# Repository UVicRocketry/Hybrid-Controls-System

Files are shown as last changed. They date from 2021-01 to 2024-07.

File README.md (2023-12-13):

# Hybrid-Controls-System (HB - Project Acronym)

## Project Information

UVic Rocketry's hybrid controls system is designed to actuate and monitor the states of stepper motor driven valves located on a high-pressure oxidizer feed system. The controls system includes the following components:
- Mission Control Board (MCB) : A physical panel with toggle switches, momentary buttons, indicator lights, and a buzzer
  - Sends commands to Mission Control Computer based on user input through switches/buttons
- Mission Control Computer (MCC) : The main controller and communication method with the valve cart
  - Manages commands from the MCB and forwards them to the valve cart 
  - Confirms valve status from the valve cart
  - Also able to be used as an override in case the MCB stops working
- Valve Control Cart (VC) : Actuates all valves on the test stand
  - Recieves command from Mission Control Computer
  - Executes valve movements
  - Obtains confirmation or error from limit switches
  - sends confirmed valve states or error back to the Mission Control Computer

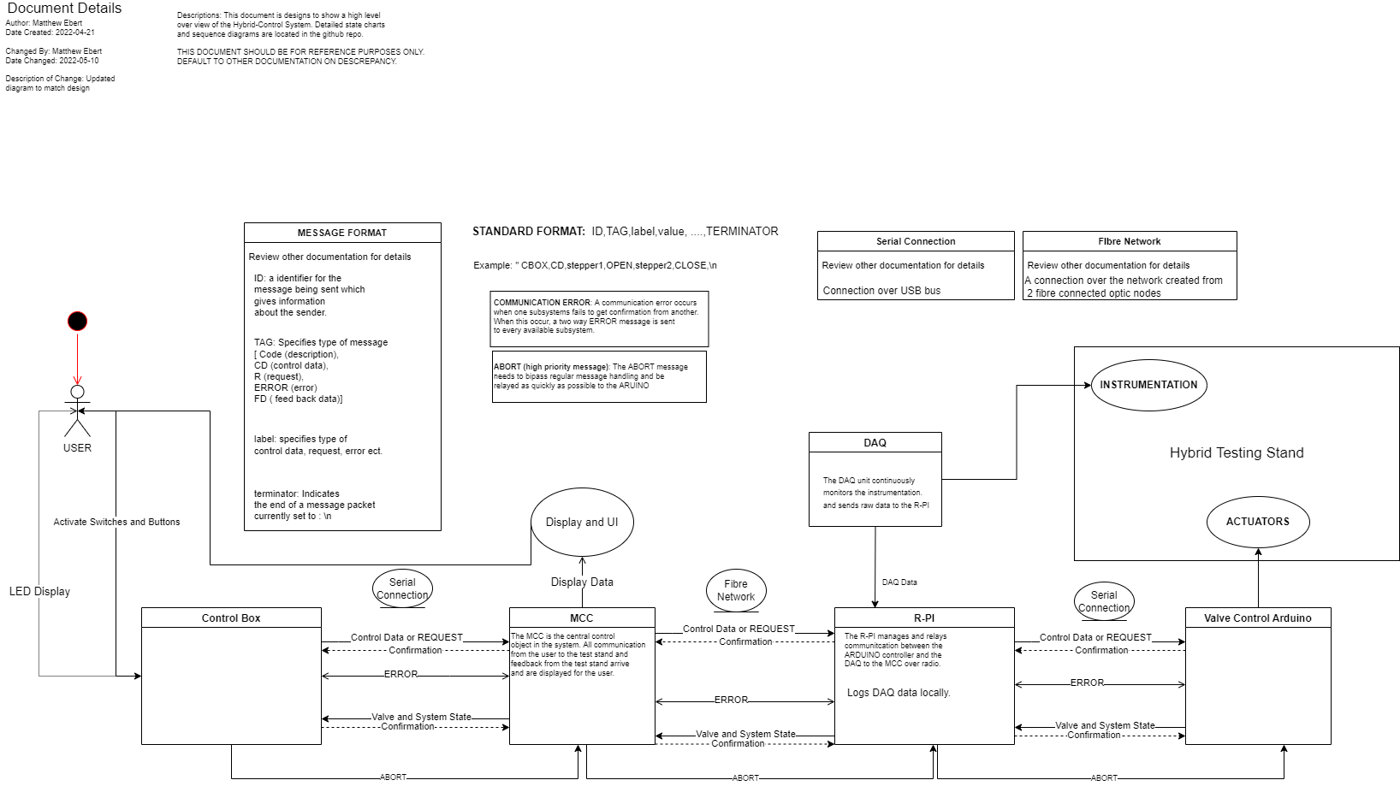
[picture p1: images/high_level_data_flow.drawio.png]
System_Control_Flow_Diagram
  
_Note: If you get the draw.io extension for vs code you can edit this picture directly._
**Possibly out of date and needs review!**

## Installation and Setup of the GUI
The GUI for the Mission Control Computer is the brains of both the Valve Cart and the Mission Control Board, as well as the communication between them. 

There are two options for installing the GUI and communication libraries: downloading a released compiled version, or downloading directly from source and running as a python script.

### Downloading and Running a Release
Releases of the GUI are bundled into a single file using PyInstaller, and built for x86_64 architecture **only**. If you need an x86 version, refer to the compiling from source instructions of this document.

1. To find the latest release, go to <https://github.com/UVicRocketry/Hybrid-Controls-System/releases> and download the executable for your system.

2. Once downloaded, you may need to enable execution of the executable (refer to your system's documentation). On Linux, this is `chmod +x HybridControlsGUI`

3. Finally, just run the GUI by either double-clicking or executing from the terminal.

### Downloading and Running from Source
Running from source is necessary if you want to be bleeding edge, or if there's no release for your system. This method is bit finicky, but if you follow the steps below, you'll be good to go

1. **Make sure you have the right Python version**, you must have Python 3.9 or above for the libraries you need to work.
2. **Install pre-requisites**: Use the following command to install all the pre-requisites you need for the GUI: `pip3 install betterconfigs pyserial PyQt5`
3. **Download from Source**: You can pull the bleeding commit from the git repo using `git pull https://github.com/UVicRocketry/Hybrid-Controls-System.git`
4. **Checkout the right branch**: Make sure you're in the right branch by cd-ing into the git repo you just downloaded and using `git checkout *branchname*` (replace branchname with the right branch name)
5. **Run the GUI**: If you've done everything right, you can run the GUI by cd'ing into `./src/MCC_GUI/` and running `python3 gui_valve.py`. If you get an error, refer to the *Common Errors* section below

## Command Structure Examples
Command structure breakdown:

VC,Command,Modifier,Modifier,etc

EX:

VC,CTRL,MEV,OPEN - opens MEV valve

VC,CTRL,N2OF,CLOSE - closes N2OF valve

VC,STATUS - reports status of all valves

VC,ABORT - initiates abort seequence

## Common Issues & Errors
**If you can open the GUI, and you're having issues with communication, use the debug console to help troubleshoot**
<details><summary>The GUI opened, but I can't see any serial devices to select</summary>
1. Is the device plugged in and receiving power? (It's okay I do it all the time too). Also, try hitting the refresh button.<br>
2. If you're getting power to the device, check the OS's device manager and see if it's showing up. If it is, you might have a permissions error with the applications. Linux especially has this issue (Your user might need to be added to the dialout group).<br>
</details>

<details><summary>I'm not able to run the GUI</summary>
Try running in your terminal and seeing if it gives you any errors. Otherwise, your window manager might not be able to run Qt applications (looking at you GTK+!)
</details>

<details><summary>Pip won't let me install the library betterconfigs</summary>
I've seen this error before, but not really sure why it happens even though the Python version is correct. You can go to PyPi and install manually if it's giving you trouble.
</details>

<details><summary>I'm not sure which branch to pull from</summary>
Ask the maintainers! If you've got access to the Discord, just message @Propulsion and someone should be able to help you out. If nobody knows, probably the latest push is the best.
</details>

<details><summary>It's still broken</summary>
If nobody in propulsion can help, contact <a href="mailto:iainrosen@uvic.ca">iainrosen@uvic.ca</a> and he should be able to help you out!
</details>

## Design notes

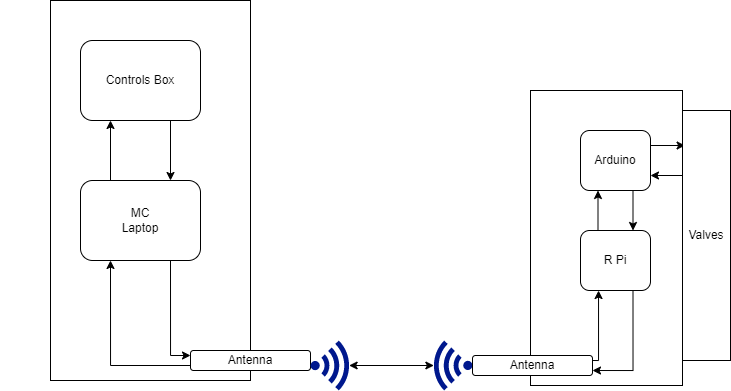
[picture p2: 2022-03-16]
images/system_diagram.png

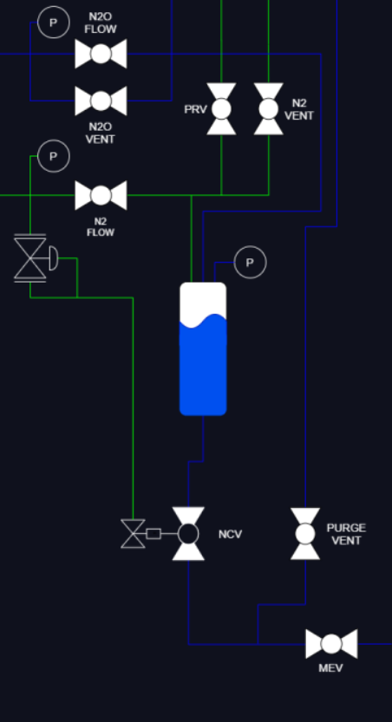
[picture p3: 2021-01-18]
images/MULE-1_PID_for_GUI.png

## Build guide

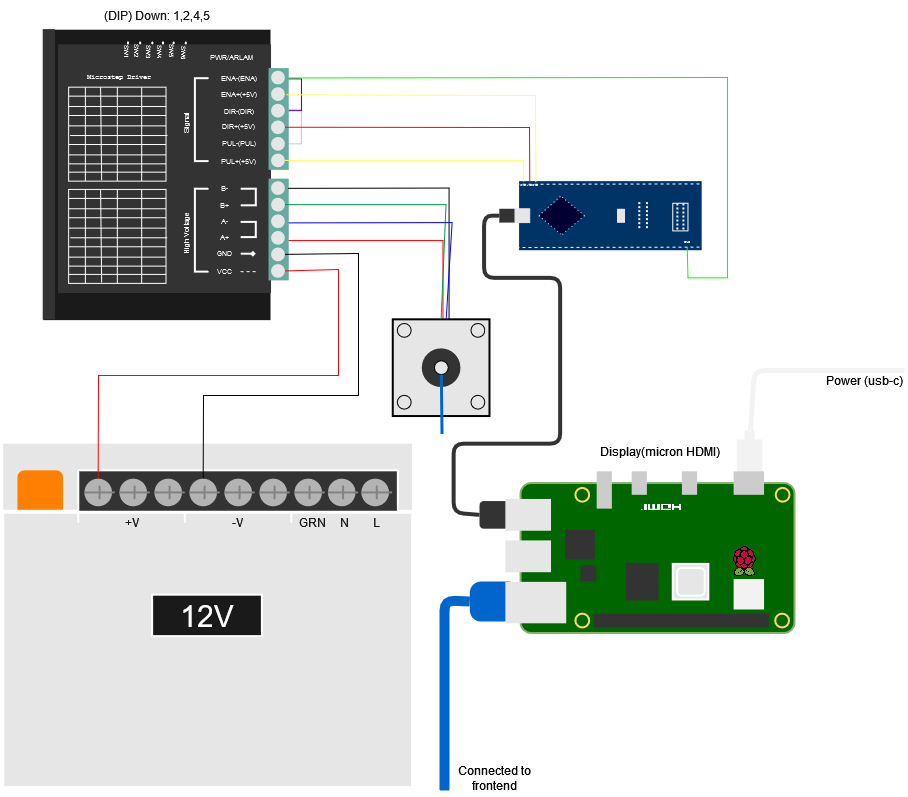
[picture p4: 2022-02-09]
images/ControlsWiringDiagram.drawio.png

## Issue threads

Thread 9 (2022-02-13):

HBPR-4 GUI Updates

Devon-H, 2022-02-13:
The following is a brief list taken from a discussion with Kris and JJ on Feb. 12, 2022.
- fix toggle switches (ask Kris Lemieux)
- Remove feed system schematic
- relocate buttons
- move mission critical buttons (Fire, abort, vent) to physical buttons
- make custom test file type for config

klemie, 2022-02-18:
Might be good to break this up into multiple issues.

Closed 2022-06-22.

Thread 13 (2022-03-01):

HBPR-7 01-03-22 Owen & Devon Meeting

Devon-H, 2022-03-01:
**Description**
Owen and Devon's meeting on March 1st.

To Do:
- organize server and client files into separate folders
- figure out what's happening on arduino side (kris knows)
- figure out what's happening on GUI side (kris knows)
-

**Acceptance Criteria**
 <Write specifically what is need for this issue to be completed>

**Dev Notes**
[for assignee]<write down your thought process when developing this issue>

**Linked issues**
 <If there are any related issues>

<Add to milestone>

Closed 2022-06-22.

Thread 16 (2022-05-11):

HBPR-8 Mission Control Box

ByonicTao, 2022-05-11:
**Description**
 Firmware for arduino with proper input gathering, comm with MCC, and data display. Along with schematic for the circuit.

**Acceptance Criteria**
 Firmware can communicate with computer properly, and display the data. Also includes an accurate schematic of the circuit.

**Dev Notes**
3rd version of LED circuit. Didn't work with back driving the switch inputs, as some LEDs would stay on  constantly and others would not turn on. Then there was discussion of wiring the LEDs up to output pins directly. This was decided against because of need to add additional things to the box, including a buzzer and potentially more signaling devices. Currently the implementation is going to use shift registers to run the LEDs which will leave plenty of room for other things to run off the digital pins and remove the flickering that would result from using an methods that uses persistence of vision.

Closed 2022-06-22.

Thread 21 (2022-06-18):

HBPR-10 On-stand Controls

OwenBC, 2022-06-18:
**Description**
 <Describe what the feature or bug that need to be resolved>
 <Description of the big component that encompasses the issue working on>
 <Depencies, ex. libraries, sensors, hardware, small parts of code youhave to work on>
 <ow to do the things>

**Acceptance Criteria**
 <Write specifically what is need for this issue to be completed>

**Dev Notes**
[for assignee]<write down your thought process when developing this issue>

**Linked issues**
 <If there are any related issues>

<Add to milestone>

Closed 2023-05-13.

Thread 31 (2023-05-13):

VCA Testing

iainrosen, 2023-05-13:
Verify the valves on the VCA are responding and moving correctly

iainrosen, 2023-06-09:
- Stepper for N20V is unresponsive, checked pin out from Arduino and all connected correctly. Limits working.

iainrosen, 2023-06-09:
Tested and working:
- N2F
- N20F
- ERV
- MEV

iainrosen, 2023-06-09:
NCV when trying to use CTRL throws a BADVAL error. Possibly not programmed for actuation?

iainrosen, 2023-06-09:
We have no way of telling where RTV is, need to talk to Devon about this.

Closed 2023-07-20.

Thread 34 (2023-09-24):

Update serial communication to new library

iainrosen, 2023-09-24:
Serial communication needs to be hauled over a bit using a new library with checksumming and implementation of duplicate message elimination

This will improve:
- Serial connections over long ranges with ethernet (which experience some issues in translation)
- Serial connections over radio, which will be used eventually to control the valve cart from afar for hot fire tests

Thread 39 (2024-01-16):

Message Parsing Issues

iainrosen, 2024-01-16:
Messages don't parse correctly, VC is sending separate format from MCC GUI

iainrosen, 2024-02-06:
The method of parsing switch states seems to be correct, going to test with the Valve Cart and see if error is replicated.

See lines 81-87 of commlib.py

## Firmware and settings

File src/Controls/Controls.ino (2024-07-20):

/*  Valve Cart and Feed System: Controls - Valve Controls - Rework V 1.1
   Author(s):
   Matthew Ebert
   Logan Sewell
   JJ
   Joshua Piuti
   Organization: UVic Rocketry
*/
#include "Valve.h"

//*********Limit Pins*********
#define OpenLimitMEV 30
#define CloseLimitMEV 27
#define OpenLimitN2OV 41
#define CloseLimitN2OV 40
#define OpenLimitRTV 39
#define CloseLimitRTV 38
#define OpenLimitN2F 42
#define CloseLimitN2F 43
#define OpenLimitERV 34
#define CloseLimitERV 35
#define OpenLimitN2OF 33
#define CloseLimitN2OF 32
#define OpenLimitNCV 28
#define CloseLimitNCV 29
//****************************

//******Enable Pins **********
#define N2OFEnab 46
#define N2OVEnab 47
#define N2FEnab 49
#define ERVEnab 50
#define MEVEnab 51

//*********Driver Pins********
#define StepMEV 19
#define DirMEV  20
#define StepN2OV 4
#define DirN2OV  3
#define StepN2F 10
#define DirN2F  9
#define StepERV 15
#define DirERV  14
#define StepN2OF 17
#define DirN2OF  16
//****************************

//***Solenoid & Igniter Pins***
#define Igniter 45
#define Solenoid 48
#define RTVEnab 37
//****************************

//*********Safety Pins********
#define KeySwitch 5
#define EStop 6
//****************************


int IgniterState = 0;
int TargetState [9];

void MoveToTarget();
void setTarget (String valveCommands);
String readCSV(String * rxBuf);
void sendState (void);

bool ABORT = false;
//Assining Valves
//Stepper Valves
Valve N2F = Valve(OpenLimitN2F, CloseLimitN2F, StepN2F, DirN2F, 20);
Valve N2OV = Valve(OpenLimitN2OV, CloseLimitN2OV, StepN2OV, DirN2OV, 4);
Valve N2OF  = Valve(OpenLimitN2OF, CloseLimitN2OF, StepN2OF, DirN2OF, 4);
Valve ERV  = Valve(OpenLimitERV, CloseLimitERV, StepERV, DirERV, 2);
Valve MEV  = Valve(OpenLimitMEV, CloseLimitMEV, StepMEV, DirMEV, 4);

//Other Valves
Valve NCV  = Valve(OpenLimitNCV, CloseLimitNCV);
Valve RTV  = Valve(OpenLimitRTV, CloseLimitRTV, RTVEnab);

void setup() {
  // Sets Limit Pins
  //enable set up
  pinMode(N2OFEnab, OUTPUT);
  pinMode(N2OVEnab, OUTPUT);
  pinMode(N2FEnab, OUTPUT);
  pinMode(ERVEnab, OUTPUT);
  pinMode(MEVEnab, OUTPUT);

  //Currently does not effect motors??
  digitalWrite(N2OFEnab, HIGH);
  digitalWrite(N2OVEnab, HIGH);
  digitalWrite(N2FEnab, HIGH);
  digitalWrite(ERVEnab, HIGH);
  digitalWrite(MEVEnab, HIGH);

  //Unsure how these operate
  pinMode(Solenoid, OUTPUT);
  digitalWrite(Solenoid, LOW);
  pinMode(Igniter, OUTPUT);
  digitalWrite(Igniter, LOW);
  //********************

  //Sets up EStop and Keyswitch
  pinMode(EStop, INPUT_PULLUP);
  pinMode(KeySwitch, INPUT_PULLUP);


  //Serial_Startup
  Serial.begin(115200);
  //time in ms the serial blocks waiting for data
  Serial.setTimeout(10);
  //*********************************************

  Serial.println("VC,STATUS,STARTUP,SUCCESS");
  Serial.println("VC,CF,Initalizing_to_safe_state:(ALL Closed)");
  sendState();
  delay(1000);
  //Set all target states to closed
  for(int i = 0; i<9; i++)
  {
    TargetState[i] = 1;
  }
}


void loop() {
  
  if (Serial.available() || digitalRead(EStop) == HIGH)
  {//if a message has been recieved
    //read all serial data
    String rxBuffer = Serial.readString();
    /*Should the buffer be cleared before entire message is sent/recieved
    a fragment will be created and not parsed. An end flag should be checked
    to ensure this case does not occur.*/
    String Command = "";
    String TYPE = "";
    String SOURCE = "";
    //read source of data
    SOURCE = readCSV(&rxBuffer);
    //read type of data
    TYPE = readCSV(&rxBuffer);
    //Send acknolodgement
    //CCSerial.println("VC,ACK,");
    /* Currently there is no error correcting or proper acknoledgement handling
    This ACK is for debugging only. Proper protocols should be developed to ensure
    a message is handled properly*/
    if (TYPE == "UNABORT" && ABORT)
    {
      Serial.println("VC,STATUS,CANCELLED ABORT");
      ABORT = false;
    } else if (TYPE == "ABORT" || ABORT == true || digitalRead(EStop) == HIGH)
    {
      ABORT = true;
      //Serial.println(TYPE);
      Serial.println("VC,STATUS,ABORTED");
      digitalWrite(Igniter, LOW);
      digitalWrite(Solenoid, LOW);

      //implement abort code
      TargetState[0] = 1;  //Close N2OF
      TargetState[1] = -1; //Open N2OV
      TargetState[2] = 1;  //Close N2F
      TargetState[3] = -1; //Open Relief Valve
      TargetState[4] = 1;  //Close MEV
      TargetState[5] = 1;  //Close RTV
      TargetState[6] = 1;  //Close Igniter
      TargetState[7] = 1;  //Close NCV
      
    } else if (TYPE == "CTRL")
    {
      //Serial.println(TYPE);
      setTarget(rxBuffer);
    } else if (TYPE == "CONNECT")
    {
      Serial.println("VC,STATUS,ESTABLISH");
      sendState();
    } else if (TYPE == "SUMMARY")
    { 
      //Serial.println(TYPE);
      sendState();
    } else
    {
      Serial.println("VC,ERROR,UNKNOWNCOMMAND," + SOURCE + "," + TYPE + "," + Command);
    }
  }

  //called every loop to step motors if necessary
  //disabled by keyswitch lockout on VC unless being aborted
  if(digitalRead(KeySwitch) == LOW || ABORT)  {
    MoveToTarget();
  }
}


/***********FUNCTIONS*******************/


void sendState (void)
{
  Serial.print("VC,SUMMARY");
  Serial.print(",N2OF," +  N2OF.strState());
  Serial.print(",N2OV," +  N2OV.strState());
  Serial.print(",N2F," +  N2F.strState());
  Serial.print(",RTV," +  RTV.solStrState());
  Serial.print(",ERV," +  ERV.strState());
  Serial.print(",MEV," +  MEV.strState());
  Serial.print(",NCV," +  NCV.strState());
  Serial.println("");
}


String readCSV (String * rxBuf)
{
  String Command = "";
  char c;
  c = (*rxBuf)[0];
  while (c != '\n' && c !=  ',' && (*rxBuf).length() > 1) {
    Command += c;
    (*rxBuf).remove(0, 1);
    c = (*rxBuf)[0];
  }
  (*rxBuf).remove(0, 1);
  return Command;
}


void setTarget (String valveCommands)
{
  String Label = "";
  String Value = "";
  int index = 0;
  while (valveCommands.length() > 1)
  {
    Label = readCSV(&valveCommands);
    Value = readCSV(&valveCommands);


    if (Label == "N2OF")
    {
    } else   if (Label ==  "N2OV")
    {
      index = 1;
    } else if (Label ==  "N2F")
    {
      index = 2;
    } else if (Label ==  "ERV")
    {
      index = 3;
    } else if (Label ==  "MEV")
    {
      index = 4;
    } else if (Label ==  "RTV")
    {
      index = 5;
    } else if (Label ==  "IGPRIME")
    {
      index = 6;
    } else if (Label == "NCV")
    {
      index = 7;
    } else
    {
      index = 8;
      Serial.println("VC,ERROR,UNKOWNVALVE");
    }

    if (Value == "OPEN")
    {
      TargetState[index] = -1;
    }
    else if (Value == "CLOSE")
    {
      TargetState[index] = 1;
    } else
    {
      TargetState[index] = 0;
    }

  }
}





void MoveToTarget()
{

  if ( N2OF.state() != TargetState[0] && TargetState[0]!=0)
  {    
    N2OF.moveStep(TargetState[0]);
  }
  if ( N2OF.getChange())
  {
    sendState();
  }

  if ( N2OV.state() != TargetState[1] && TargetState[1]!=0)
  {
   N2OV.moveStep(-TargetState[1]);
  }
  if ( N2OV.getChange())
  {
    sendState();
  }

  if ( N2F.state() != TargetState[2] && TargetState[2]!=0)
  {
    N2F.moveStep(TargetState[2]);
  }
  if ( N2F.getChange())
  {
    sendState();
  }

  if ( ERV.state() != TargetState[3] && TargetState[3]!=0)
  {
    ERV.moveStep(-TargetState[3]);
  }
  if ( ERV.getChange())
  {
    sendState();
  }

  if ( MEV.state() != TargetState[4] && TargetState[4]!=0)
  {
    MEV.moveStep(-TargetState[4]);
  }
  if ( MEV.getChange())
  {
    sendState();
  }


  if (RTV.solState() != TargetState[5] && TargetState[5]!=0)
  {
    RTV.moveSol(TargetState[5]);   
    sendState();     
  }
  
  if (IgniterState != TargetState[6] && TargetState[6]!=0)
  {
    if (TargetState[6] == 1)
    {
      digitalWrite(Igniter, LOW);
      IgniterState = 1;
    } else if (TargetState[6] == -1) {
      digitalWrite(Igniter, HIGH);
      IgniterState = -1;
    }
  }

  if (NCV.state() != TargetState[7] && TargetState[7]!=0)
  {
    if (TargetState[7] == 1)
    {
      digitalWrite(Solenoid, LOW);
    } else if (TargetState[7] == -1)
    {
      digitalWrite(Solenoid, HIGH);
    }
  }
  if (NCV.getChange())
  {
    sendState();
  }
}

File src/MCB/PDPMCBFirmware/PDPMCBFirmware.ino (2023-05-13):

/* UVR Propulsion Development Platform Mission Control Box Firmware
  Matthew Ebert
  2023-FEB-01

  This firmware controls the mission control box, gathering input from the switches and buttons, sending them to the controls computer

  This program only sends data on a STATE CHANGE.

  Limited logic should be implemented here.
  The idea is to create a simple controller for the attached computer (MCC)
*/


/***************DEFINITIONS ******************/


/*************PINS and MASKS**************/
#define pinBUZ 11
#define pinABORT 2
#define maskABORT (1<<pinABORT)
#define pinARMKEY 3
#define maskARMKEY 1<<pinARMKEY
#define pinIGFIRE 4
#define maskIGFIRE (1<<pinIGFIRE)
#define pinIGPRIME 5
#define maskIGPRIME (1<<pinIGPRIME)
#define maskPC 0x3F
#define maskPD 0xF0



/**************STRING OUTPUT FORMAT*******************/
#define numValves 9
String listValves[numValves] = {"MEV", "IGPRIME", "IGFIRE", "EVV", "NCV", "RTV", "N2F", "N2OV", "N2OF"};
//String listValves[numValves] = ("N2OF", "N2OV", "N2F", "RTV", "NCV", "EVV", "IGPRIME", "IGFIRE", "MEV");

/****************TYPES******************/
enum status_t {
  DISARMED,//0
  ARMED,//1
};


/**************GLOBALS****************/

volatile bool ABORT = false;
volatile status_t CurSTATUS = NULL;
volatile uint16_t CurState = NULL;




void setup() {
  Serial.begin(115200);
  
  while (!Serial) {};

  Serial.setTimeout(100);
  Serial.flush();
  Serial.print("MCB,STATUS,STARTUP\n");
  cli();
  //sets pinmodes
  DDRD = 0x00;
  DDRC = 0x00;
  DDRB |= 0x04;
  digitalWrite(11, 0);
  abortSetup();
  buzzerSetup();

  PCICR |= B00000100; // Enable interrupts on PD port
  PCMSK2 |= B00101000;
  sei();
  delay(100);
}//setup




void loop()
{

  CurState = getState();
  uint16_t NewState = CurState;
  CurSTATUS = getSTATUS();
  if (CurSTATUS == DISARMED) Serial.print("MCB,STATUS,DISARMED\n");
  if (CurSTATUS == ARMED)
  {
    Serial.print("MCB,STATUS,ARMED\n");
    sendStates(NewState);
  }
  status_t NewSTATUS = CurSTATUS;



  while (!ABORT)
  {


    if (Serial.read() > 0)
    {
      if (CurSTATUS == DISARMED)
      {
        if (CurSTATUS == DISARMED) Serial.print("MCB,STATUS,DISARMED\n");
        return;
      } else
      {
        if (CurSTATUS == ARMED) Serial.print("MCB,STATUS,ARMED\n");
        sendStates(CurState);
      }
   
    }

    NewSTATUS = getSTATUS();
    delay(50);//debounce
    if (NewSTATUS == getSTATUS())
    {
      if (NewSTATUS != CurSTATUS)
      {
        CurSTATUS = NewSTATUS;
        if (CurSTATUS == DISARMED) Serial.print("MCB,STATUS,DISARMED\n");
        if (CurSTATUS == ARMED) Serial.print("MCB,STATUS,ARMED\n");
      }//IF CHANGE STATUS
    }//IF DEBOUNCE



    if (CurSTATUS)
    {
      NewState = getState();
      delay(50);//debounce
      if (NewState == getState())
      {
        if ((NewState != CurState))
        {
          if (getSTATUS())
          {
            sendStates(NewState);
            CurState = NewState;
          }
        }//IF CHANGE STATE
      }//IF DEBOUNCE
    }//IF STATUS

    
  }//WHILE !ABORT




//When ABORT PRESSED
  while (1)
  {
    Serial.print("MCB,ABORTED\n");
    delay(100);
  }

}//loop


//Functions
//-----------------------------------------------------------------------------------------------


uint16_t getState(void)
{
  uint16_t state = ((PIND & maskPD) >> 4) + ((PINC & maskPC) << 4);
  //Serial.print("Registers: ");
  //Serial.println(state);
  return state;
}


status_t getSTATUS(void)
{
  if ((PIND & maskARMKEY) == 0)
  {
    return ARMED;
  } else
  {
    return DISARMED;
  }
}



void sendStates(uint16_t tempState)
{
  Serial.print("MCB,SUMMARY,");

  for (int i = 0; i < numValves; i++)
  {
    Serial.print(listValves[i]);
    Serial.print(",");
    if (tempState & 0x01)
    {
      Serial.print("CLOSE");
    } else
    {
      Serial.print("OPEN");
    }
    tempState = tempState >> 1;
    if(!(i==numValves-1)){
      Serial.print(",");
    }
    
  }
  Serial.print("\n");
}



void abortSetup(void)
{

  EIMSK |= 0x01;//Enable INT0 on D2
  EICRA |= _BV(ISC00) | _BV(ISC00);

}

void buzzerSetup(void)
{
 
  TCCR1A = 0;// set entire TCCR1A register to 0
  TCCR1B = 0;// same for TCCR1B
  TCNT1  = 0;//initialize counter value to 0
  // set compare match register for 1hz increments
  OCR1A = 10000;
  // turn on CTC mode
  TCCR1B |= _BV(WGM12);
  // Set CS10 and CS12 bits for 1024 prescaler
  // TCCR1B |= (1 << CS12) | (1 << CS10);
  // enable timer compare interrupt
  TIMSK1 |= _BV(OCIE1A);
}


ISR(TIMER1_COMPA_vect)
{
  analogWrite(11, 0);
  TCCR1B &= !_BV(CS12) & !_BV(CS10);
}


ISR (PCINT2_vect) {
  delay(50);
  if ((PIND & maskIGPRIME) == 0)
  {
    digitalWrite(pinBUZ, 1);
    TCNT1 = 0;
    TCCR1B |= _BV(CS12) | _BV(CS10);
  }

  
  if (((PIND & maskARMKEY) == 0) && (CurSTATUS == DISARMED))
  {
    digitalWrite(pinBUZ, 1);
    TCNT1 = 0;
    TCCR1B |= _BV(CS12) | _BV(CS10);
  }
}


ISR(INT0_vect)
{

  for (int i = 0; i < 1000; i++)
  {
    if ((PIND & maskABORT) == 0)
    {
      return;
    }
  }
  if ((PIND & maskABORT) > 0)
  {
    ABORT = true;
    Serial.print("MCB,ABORT,\n");
    digitalWrite(pinBUZ, 1);
    TCNT1 = 0;
    TCCR1B |= _BV(CS12) | _BV(CS10);
  }
}

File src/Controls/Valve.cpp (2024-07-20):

#include "Arduino.h"
#include "Valve.h"

// Constructor
Valve::Valve(int OpenLimit, int CloseLimit) {
  this->OpenLimit = OpenLimit;
  this->CloseLimit = CloseLimit;
  this->change = 0;
  this->prevState = 0;//!digitalRead(OpenLimit) | !digitalRead(CloseLimit);
  pinMode(OpenLimit, INPUT_PULLUP);
  pinMode(CloseLimit, INPUT_PULLUP);
}

Valve::Valve(int OpenLimit, int CloseLimit, int StepPin, int DirPin, int StepSpeed) {
  this->OpenLimit = OpenLimit;
  this->CloseLimit = CloseLimit;
  this->StepPin = StepPin;
  this->DirPin = DirPin;
  this->StepSpeed = StepSpeed;
  this->change = 0;
  this->prevState = 0;//!digitalRead(OpenLimit) | !digitalRead(CloseLimit);
  pinMode(OpenLimit, INPUT_PULLUP);
  pinMode(CloseLimit, INPUT_PULLUP);
  pinMode(DirPin, OUTPUT);
  pinMode(StepPin, OUTPUT);
  StepTime = millis();
}

Valve::Valve(int OpenLimit, int CloseLimit, int SolEnab) {
  this->OpenLimit = OpenLimit;
  this->CloseLimit = CloseLimit;
  this->SolEnab = SolEnab;
  this->change = 0;
  this->activated = 1;
  this->prevState = 0;//!digitalRead(OpenLimit) | !digitalRead(CloseLimit);
  pinMode(OpenLimit, INPUT_PULLUP);
  pinMode(CloseLimit, INPUT_PULLUP);
  pinMode(SolEnab, OUTPUT);
  digitalWrite(SolEnab, LOW);  
}

//*********State functions*********
int Valve::state() {
  if (digitalRead(OpenLimit) == LOW) {
    change = (prevState != -1);
    prevState = -1;
    return -1;
  } else if (digitalRead(CloseLimit) == LOW) {
    change = (prevState != 1);
    prevState = 1;
    return 1;
  } else {
    change = (prevState != 0);
    prevState = 0;
    return 0;
  }
}

int Valve::solState() {
  if(activated == 1) {
    change = (prevState != 1);
    prevState = 1;
    return 1;
  } else if (activated == -1) {
    change = (prevState != -1);
    prevState = -1;
    return -1;
  } else {
    change = (prevState != 0);
    prevState = 0;
    return 0;
  }
}

String Valve::strState() {
  if (digitalRead(OpenLimit) == LOW) {
    change = (prevState != -1);
    prevState = -1;
    return "OPEN";
  } else if (digitalRead(CloseLimit) == LOW) {
    change = (prevState != 1);
    prevState = 1;
    return "CLOSE";
  } else {
    change = (prevState != 0);
    prevState = 0;
    return "TRANSIT";
  }
}

String Valve::solStrState() {
  if(activated == 1) {
    change = (prevState != 1);
    prevState = 1;
    return "CLOSE";
  } else if (activated == -1) {
    change = (prevState != -1);
    prevState = -1;
    return "OPEN";
  } else {
    change = (prevState != 0);
    prevState = 0;
    return "TRANSIT";    
  }
}

bool Valve::moveStep(int Dir)
{ 
  //Serial.print("Stepping Pin:");
  //Serial.println(StepPin);
  if ((millis() - StepTime) > StepSpeed)
  {
    //Serial.println(millis());
    //Serial.println(StepTime);
    //Serial.println(millis()-StepTime);
     if(Dir==1)
    {
       digitalWrite(DirPin, 1);
    }else
    {
      digitalWrite(DirPin, 0);
    }
    delayMicroseconds(50);
    digitalWrite(StepPin, 1);
    delayMicroseconds(50);
    digitalWrite(StepPin, 0);
    StepTime=millis();
    return true;
    
  }else if(StepTime>millis())
  {
    //overflow of 32bit millis number
    StepTime=millis();
  }
  return false;
}

bool Valve::moveSol(int State)
{
  if (State == 1)
  {
    digitalWrite(SolEnab, 0);
    activated = 1;
  } else
  {
    digitalWrite(SolEnab, 1);
    activated = -1;
  }
  return true;
}

//*********Getters*********
int Valve::getOpenLimit() {
  return this->OpenLimit;
}

int Valve::getCloseLimit() {
  return this->CloseLimit;
}


int Valve::getChange() {
  return change;
}

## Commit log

2020-10-17 created the framework of the controller file
2020-10-22 Buttons update system states. GUI Fixes
2020-12-18 Controller receiver class implementation
    Created the receiver class in controller.py, this will be in charge of connecting to, and sending and receiving data form the server
2020-12-31 Added manual checkboxs backend and schematic files
2021-01-11 Added AUTO control buttons and bugfixes
2021-01-15 Changed check boxes to toggle switches
2021-01-29 Added the state update method and thread.
2021-02-04 Changed VV to N2 flow
2021-02-23 Fixes schematic png
2021-02-27 Quick exception catch
    Fixed an error in server.py that caused the thing to crash when you hit the disconnect button
2021-03-04 setup for arduino file
2021-03-04 flash LED
2022-02-09 Arduino changes
2022-02-18 arduinoController structure see PR comment
2022-03-16 Revised control logic overview
    Now encompasses the whole system. Still needs a lot of work to properly document what's happening at every stage in the system.
2022-05-10 Updated ReadME and added design diagrams
    Added design diagrams to .source/images folder. Update read me to current design intentions.
2022-05-11 Changed Folder Structure and added requirements documents
    [HCS_Requirements_Documentation.xlsx]
2022-05-11 Added firmware and circuit schematic
    [PDPMCBCircuit.kicad_pcb, PDPMCBCircuit.kicad_sch, PDPMCBCircuit.sch]
2022-05-11 Removing Redundant Directory
    [PDPMCBCircuit.kicad_pcb, PDPMCBCircuit.kicad_sch, PDPMCBCircuit.sch]
2022-05-11 Adding removed files back in
    [PDPMCBCircuit.kicad_pcb, PDPMCBCircuit.kicad_sch, PDPMCBCircuit.sch]
2022-05-11 Added Labels to circuit
    [PDPMCBCircuit.kicad_sch]
2022-05-13 LEDs displaying switch status correctly
    [PDPMCBFirmware.ino]
2022-05-16 Added Igniter Sequence and update Request DAQ sequence
    [HCS_Requirements_Documentation.xlsx]
2022-05-17 Updated ReadME and requirements documentation
    [HCS_Requirements_Documentation.xlsx]
2022-05-31 commenting, compliance, schematic update
    Added commenting to MCB firmware code, updated outputs for compliance with communication standard, updated schematic for adjusted circuit
    [PDPMCBCircuit.kicad_sch]
2022-05-31 fixed bugs and added arming key
    [PDPMCBFirmware.ino]
2022-05-31 added buzzer code, testing flag
    [PDPMCBFirmware.ino]
2022-06-03 Updated Read me COMS, and tests in Requirements documents
    Added CF to list of tags
    Added tests for sub systems
    [HCS_Requirements_Documentation.xlsx]
2022-06-06 Bug Fixes from testing session
    [PDPMCBFirmware.ino]
2022-06-07 got comms working, fixed shift register logic
    [PDPMCBFirmware.ino]
2022-06-18 test thread
2022-07-02 Restructured added ARD controller
    [PDPMCBCircuit.kicad_pcb, PDPMCBCircuit.kicad_sch, PDPMCBCircuit.sch]
2023-02-02 Deleted old files
    Deleted out of date docs
    [HCS_Requirements_Documentation.xlsx]
2023-02-02 Started new design for MCB electrical
    [PDPMCBCircuit.kicad_sch]
2023-02-03 Updated Firmware for MCB
    Implemented an array of active low switches, an interrupt for ARMKEY, and interrupt for ABORT
    [PDPMCBCircuit.kicad_sch]
2023-02-04 Finished electrical Schematic and Code to include all valves
    [PDPMCBCircuit.kicad_sch]
2023-02-07 Cleanup and stability improvements
    [gui_valve.py, vc_runtime.ino]
2023-02-08 Working Version
    Finished a working version of the code
    [PDPMCBCircuit.kicad_sch]
2023-02-12 Fixed abort and buzzer bugs
    [PDPMCBCircuit.kicad_sch]
2023-02-14 Prep for valve control code
2023-02-27 Redesign PortSel and Debug
    [gui_valve.py]
2023-03-01 Added dictionary-like lookup for valve states
2023-03-01 Moved comm libraries into one file for all devices
2023-03-01 Changed exit code to prevent non-0 exit
    [comm.py]
2023-03-05 Implemented new version of VC control
    This version does not block any states and sends status on valve change.
    No interrupts are in use due to current pin assignments
2023-03-28 Update Valve
    Ready for testing
2023-04-01 Revert "Compatibility for MCB"
    This reverts commit d77529d38edbe7b8d6467a805cdf820481b379c5.
    Committed to wrong branch
    [PDPMCBFirmware.ino, comm.py, gui_valve.py]
2023-04-05 Fixed stepper count overflow
    [Controls.ino, Valve.cpp]
2023-04-05 Operational for all Stepper Motors
2023-05-12 Better cleanup of loose threads when quitting GUI
    [gui_valve.py]
2023-07-20 Fixed N2OV Valve
    Fixed issue disabling N2OV valve by removing comment
    [Controls.ino]
2023-07-20 Revert "Fixed N2OV Valve"
    [Controls.ino]
2023-07-29 Solenoid Implementation
    Added solenoid for NCV
2023-07-31 Added RTV & Igniter function
    Fixed RTV function for new hardware, fixed igniter relay function, added UNABORT command for recovery of system after ABORT.
    [Controls.ino]
2023-11-03 Valve Fixes
    Fixed ERV direction and limit switch definitions. Changed N2OV step and dir pins to fix issue.
    [Controls.ino]
2024-01-14 Comm Prot Fixes
    Various comms protocol changes to work with MCC_GUI script
    [Controls.ino]
2024-02-06 Added disable desync button
2024-02-18 GUI and VC can communicate
    Changes from troubleshooting GUI and VC to get them to work together. Added commas to end of GUI messages as they were being truncated for some reason. Cleaned up old files that were adding confusion. Fixed out of bounds error when parsing Summary input. Added new solenoid valve class to allow for RTV to function with GUI.
    Also added functionality for EStop and Key Switch on VC.
    [Controls.ino, Valve.cpp, comm.py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]
2024-03-12 Revert "Troubleshooting MCB"
    This reverts commit 06be5ead44193b3d809d6f638f397ec573da2825.
    [PDPMCBFirmware.ino]
2024-07-20 july pre cold flow pin reassignment
